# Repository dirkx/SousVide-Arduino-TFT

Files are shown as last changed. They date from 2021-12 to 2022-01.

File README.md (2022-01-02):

# Sousvide controller

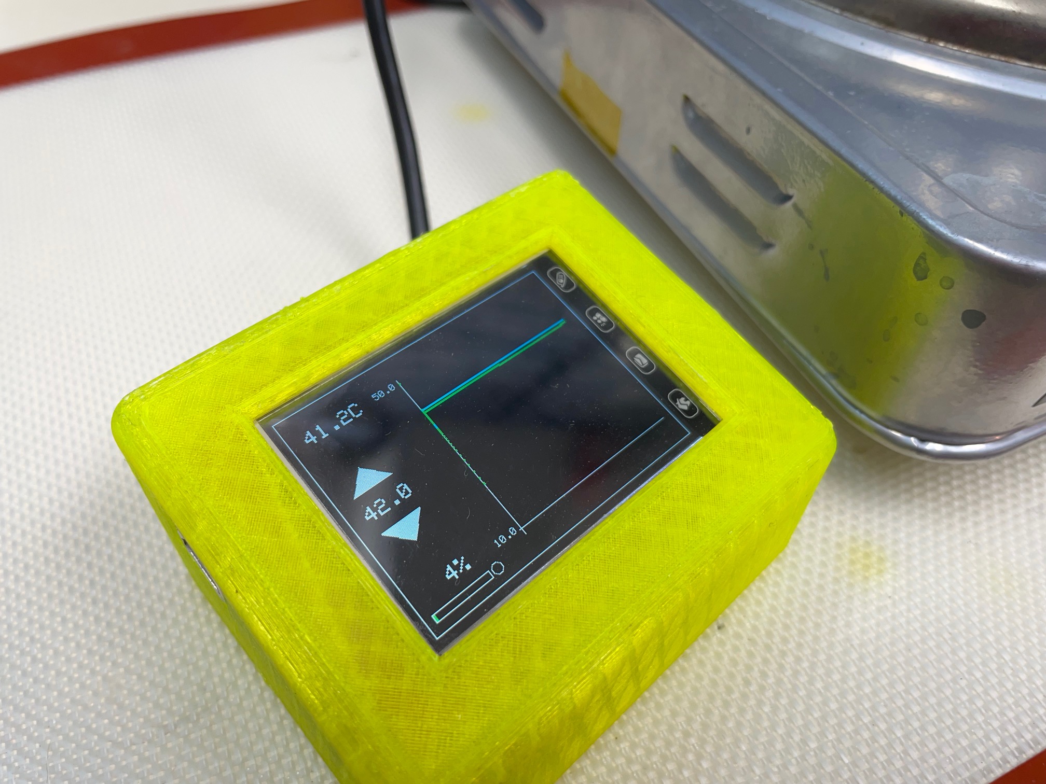
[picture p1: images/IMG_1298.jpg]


# Parts/Bill of material

Prices shown below are just the `first hit` on duckduckgo; if you shop around a bit - you may well get much lower prices on Aliexpress.

1. Hotplate, € 9.99 https://www.obelink.nl/tristar-kp-6185-kookplaat.html
2. Solid state relay € 5-10 euro; 16 Ampere https://www.amazon.nl/-/en/dp/B09F9WK7JP/ref=sr_1_14
3. Arduino UNO https://www.kiwi-electronics.nl/nl/arduino-uno-rev3-atmega328-729
4. 2.4 inch TFT screen € 5-10 https://www.aliexpress.com/item/32923876240.html
5. Waterproof Temperature sensor: € 2-5 https://www.hobbyelectronica.nl/product/ds18b20-waterdicht/ or alternatively the https://www.amazon.nl/MAX6675-Temperatuur-Thermokoppel-Schroef-Arduino/dp/B07Y9YJ3HG/ref=sr_1_5 for a wider range.
6. Some 5 volt adaptor € 2-3 https://nl.aliexpress.com/item/1005001863054181.html
7. Any 10-22 k resistor (1/16 watt or more)
 
# Wiring

The trick here is that we continue use the original knob and temperature safeties. So these still set a 'max'.

## before

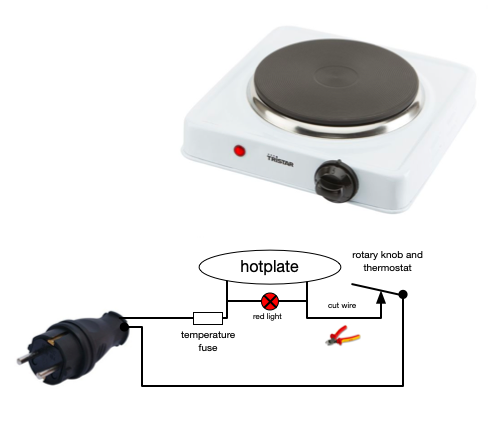
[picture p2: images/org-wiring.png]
Wiringt Wiring before


The intend is to also snip, rather than bypass or bridge, the origianal termo controlled switch.

## after
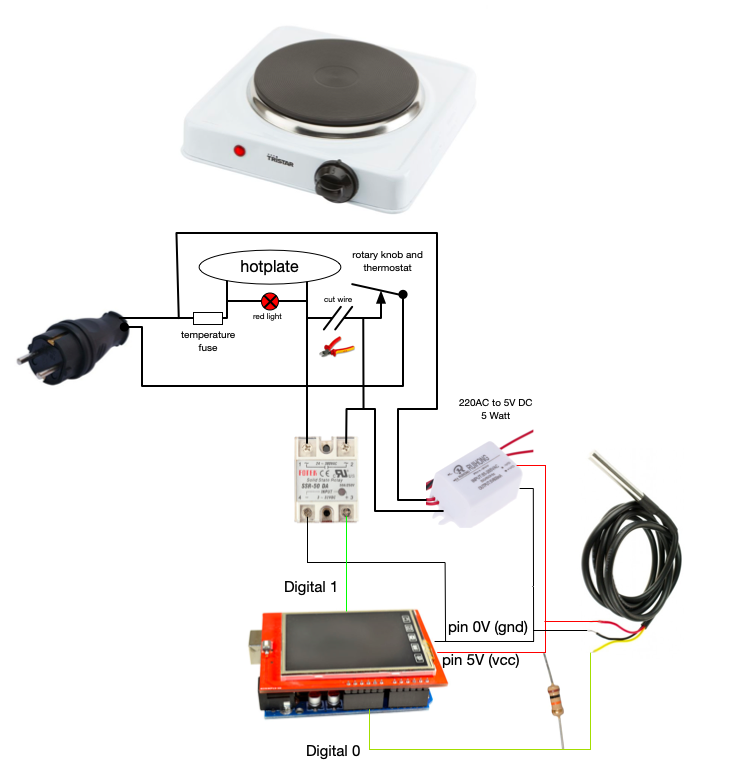
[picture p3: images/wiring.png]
Wiringt Wiring after


When mounting the SSR inside the case - note that there is one area that is nicely 'flat' (under the sticker). So it is best to mount here; as that means that the whole casing becomes a bit of a heatsink too.

# Enclosure

## OpenSCAD version

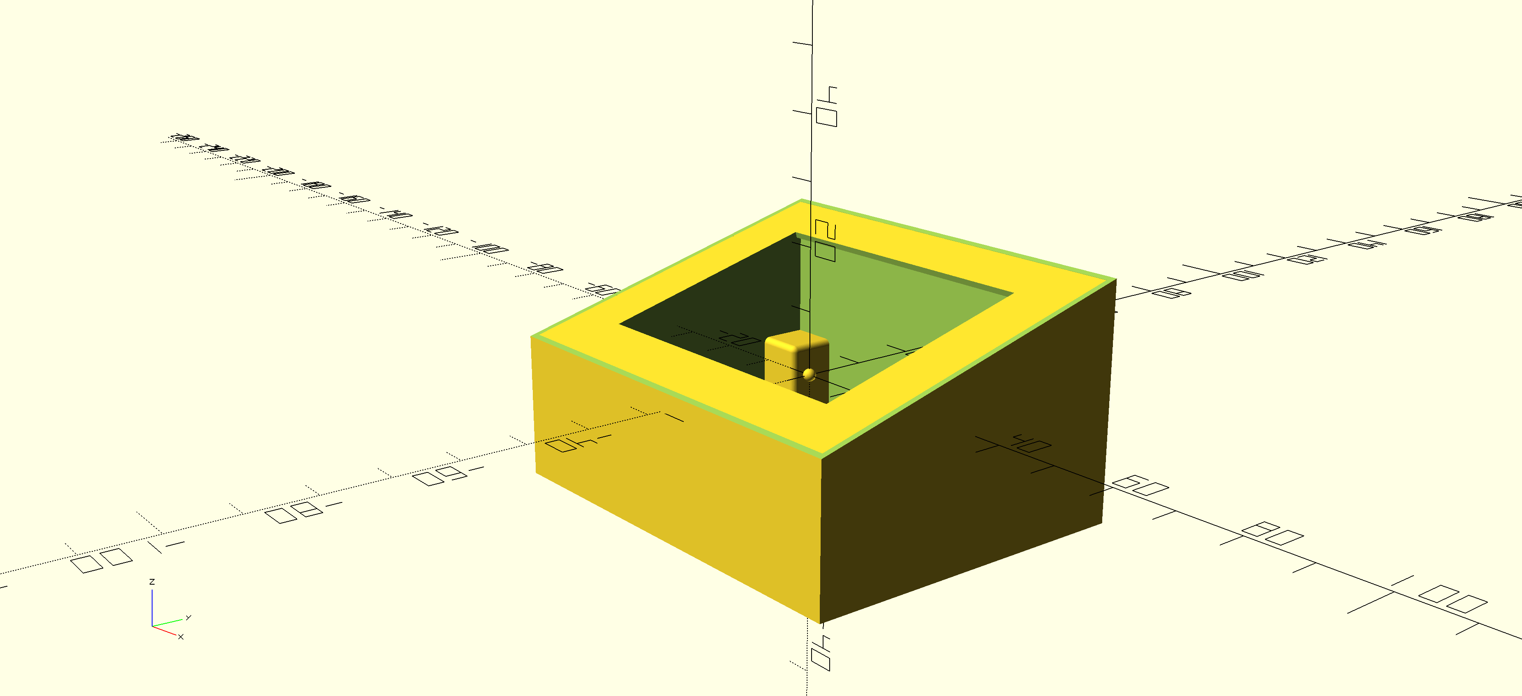
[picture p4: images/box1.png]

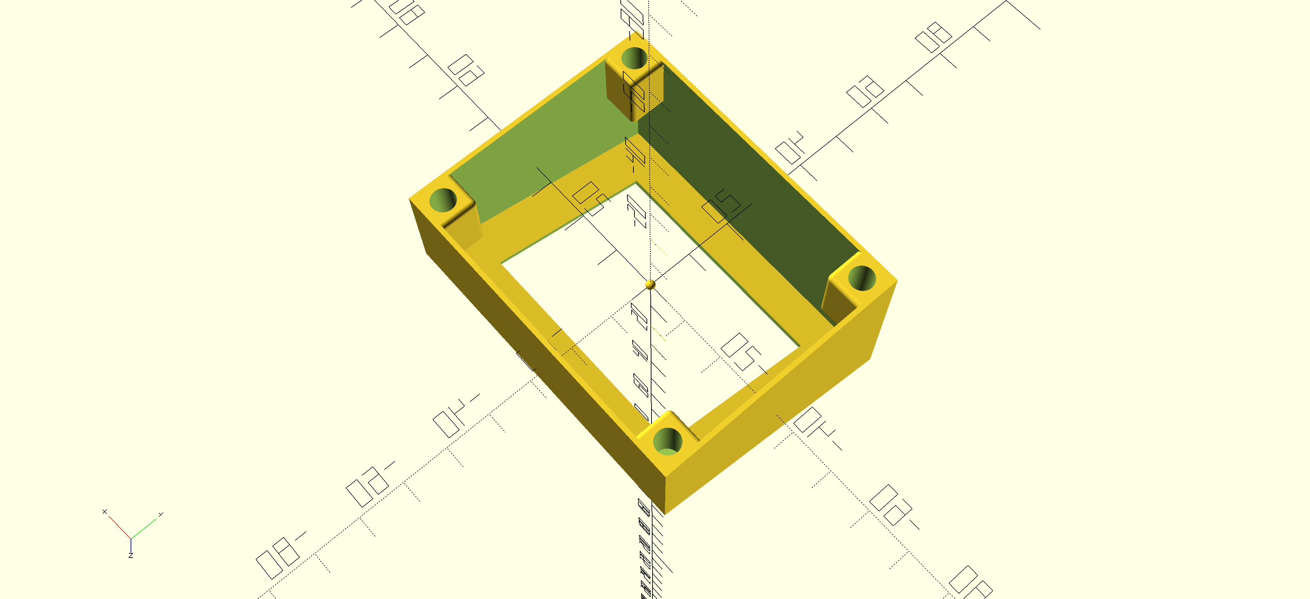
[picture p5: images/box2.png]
Box botom Box bottom


## STEP/Fusion version

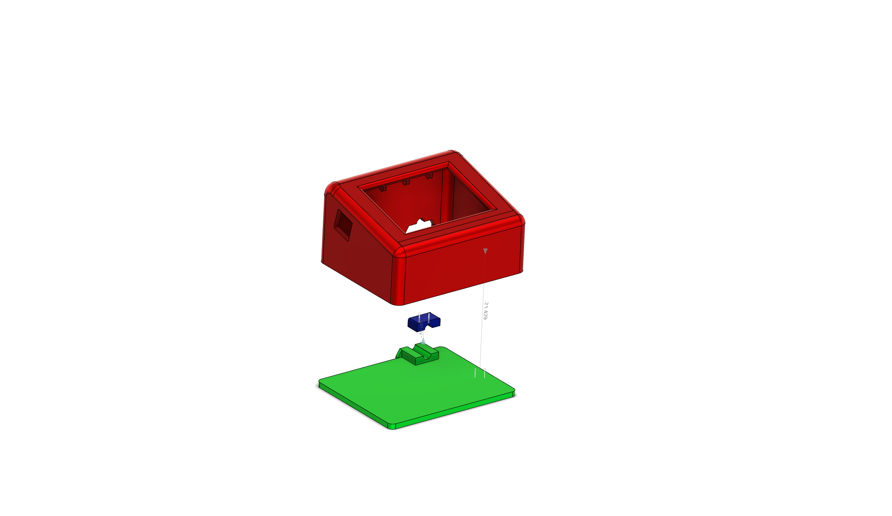
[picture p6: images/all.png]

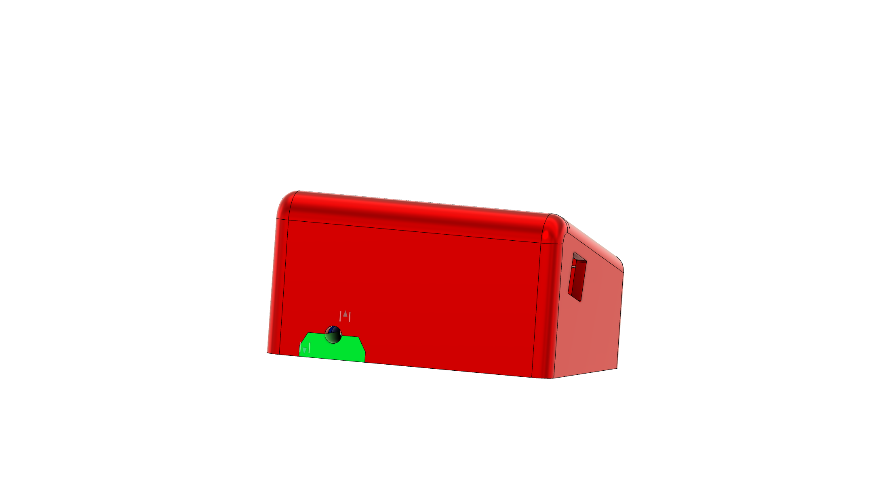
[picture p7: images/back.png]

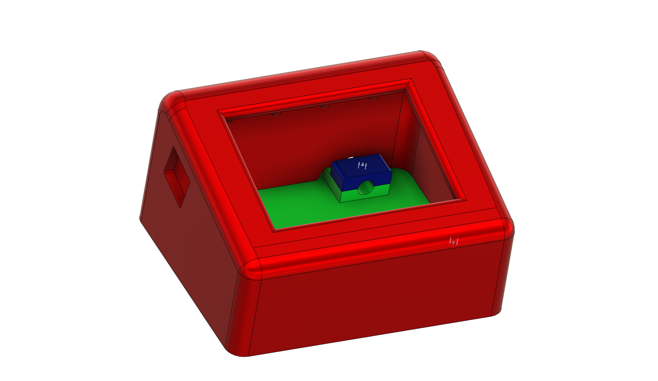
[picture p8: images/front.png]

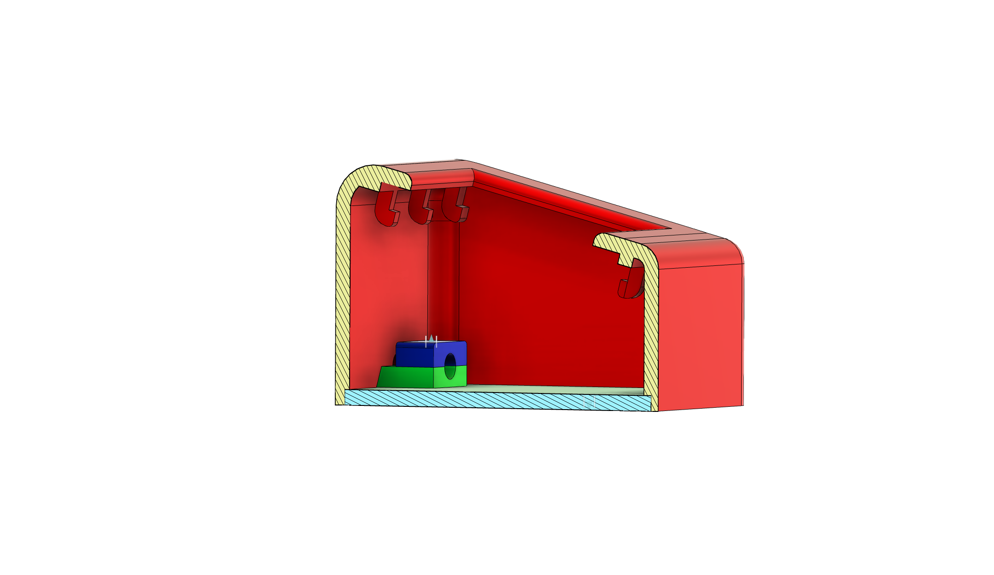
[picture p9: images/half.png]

Box top
Box top

# Result

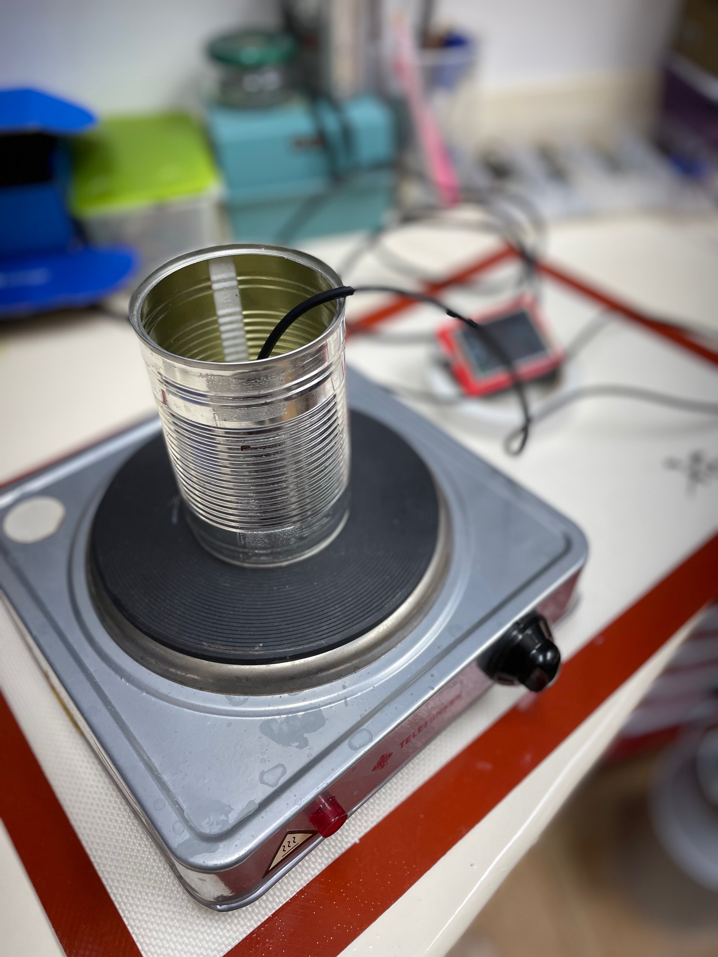
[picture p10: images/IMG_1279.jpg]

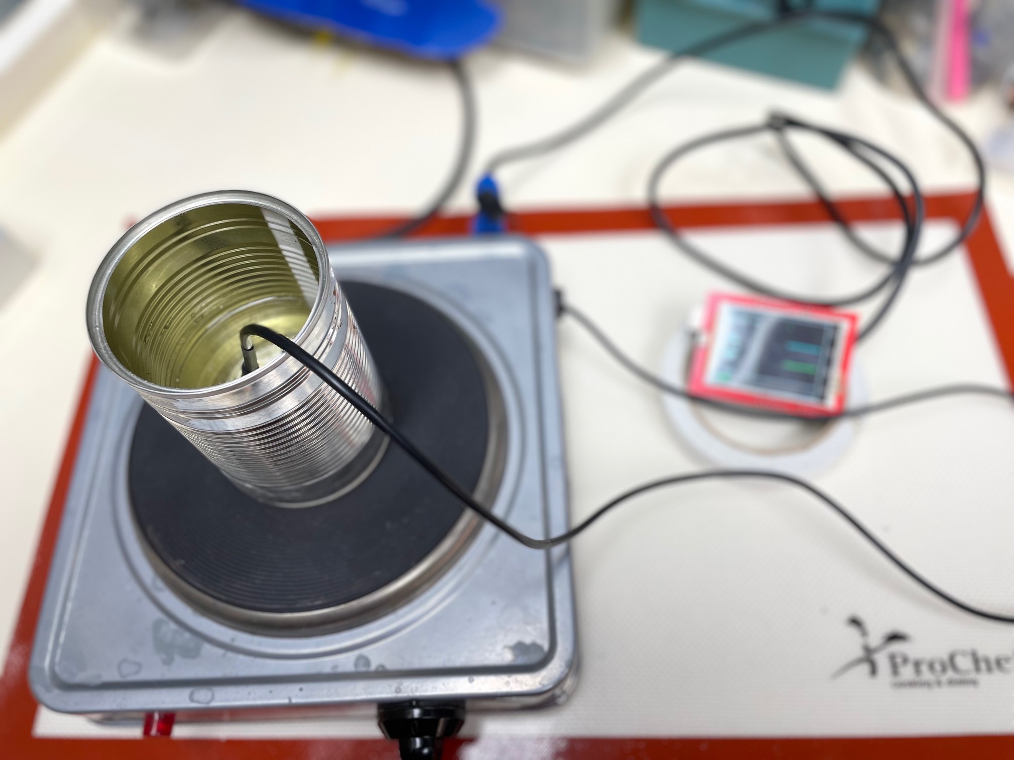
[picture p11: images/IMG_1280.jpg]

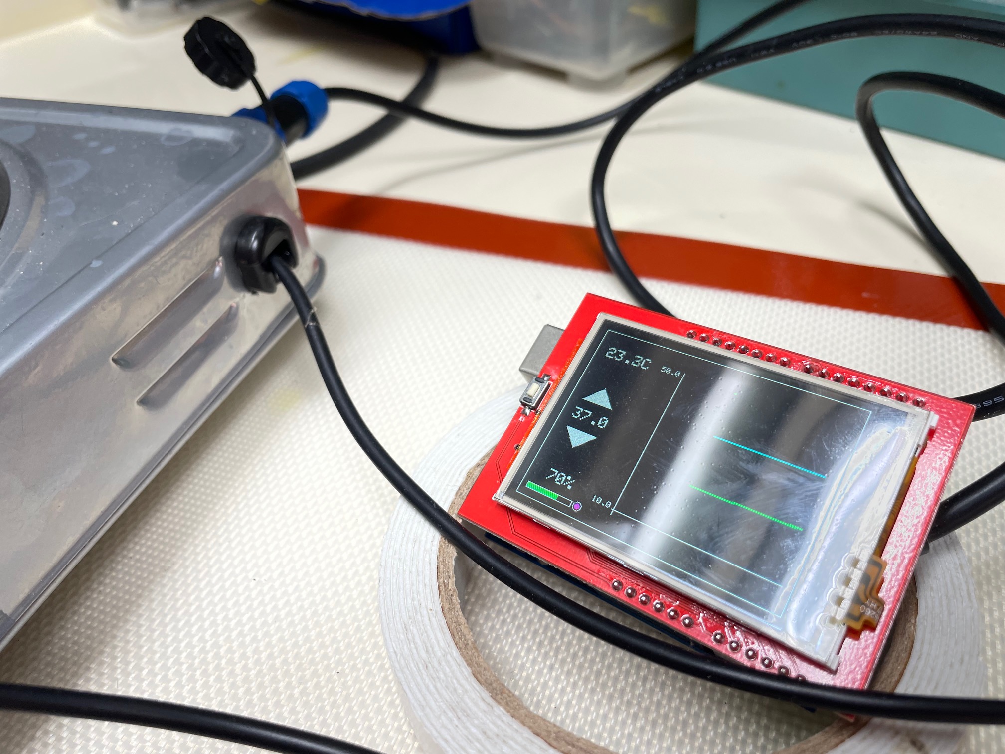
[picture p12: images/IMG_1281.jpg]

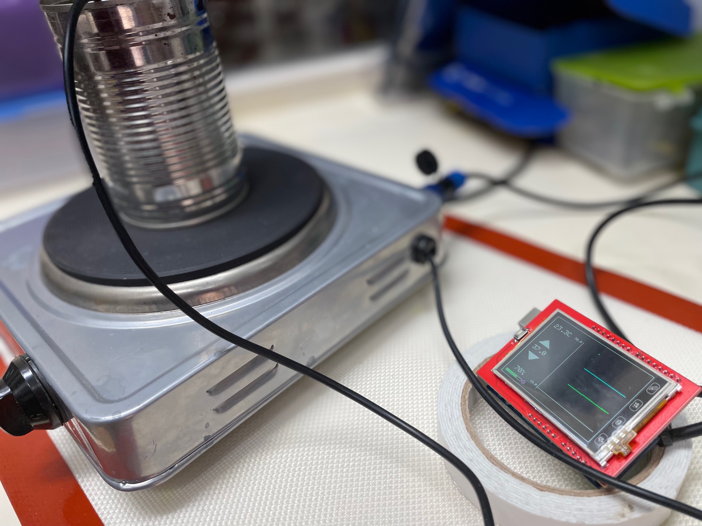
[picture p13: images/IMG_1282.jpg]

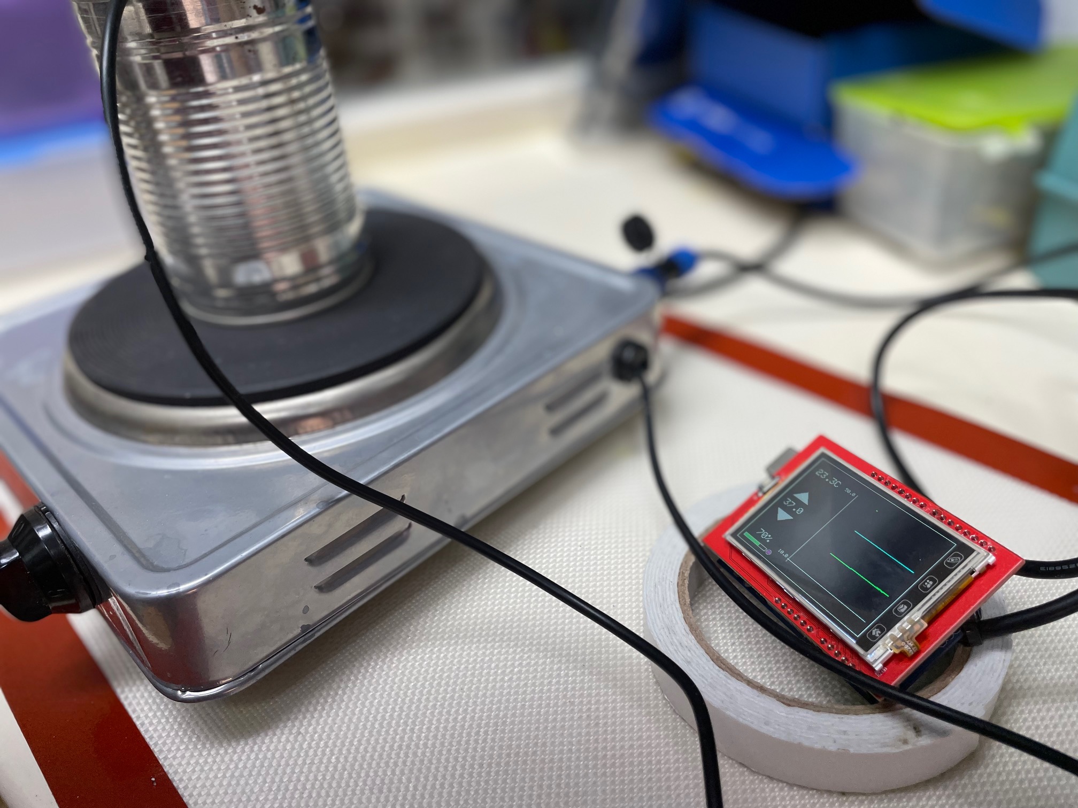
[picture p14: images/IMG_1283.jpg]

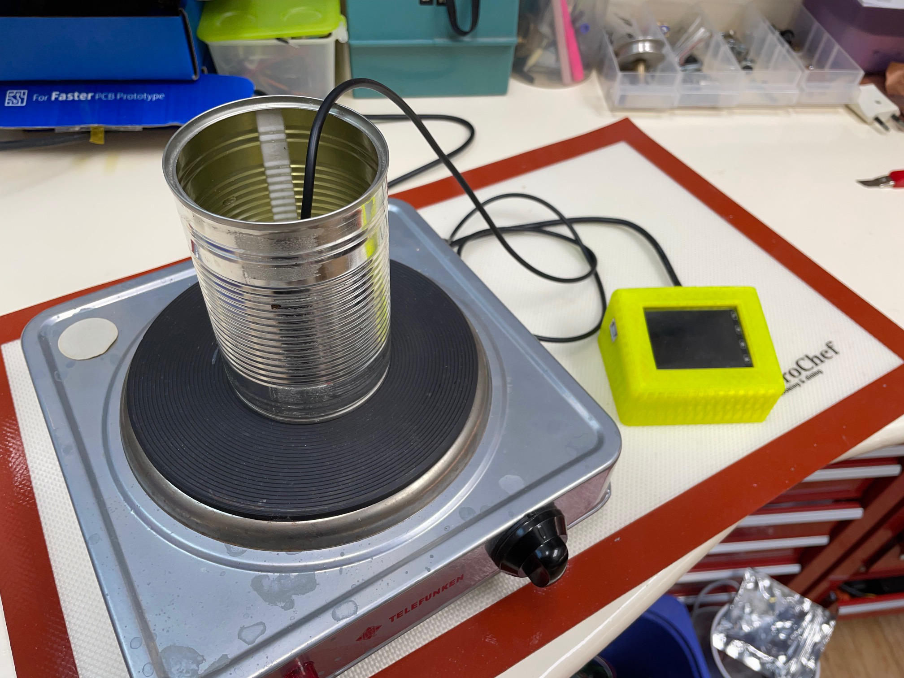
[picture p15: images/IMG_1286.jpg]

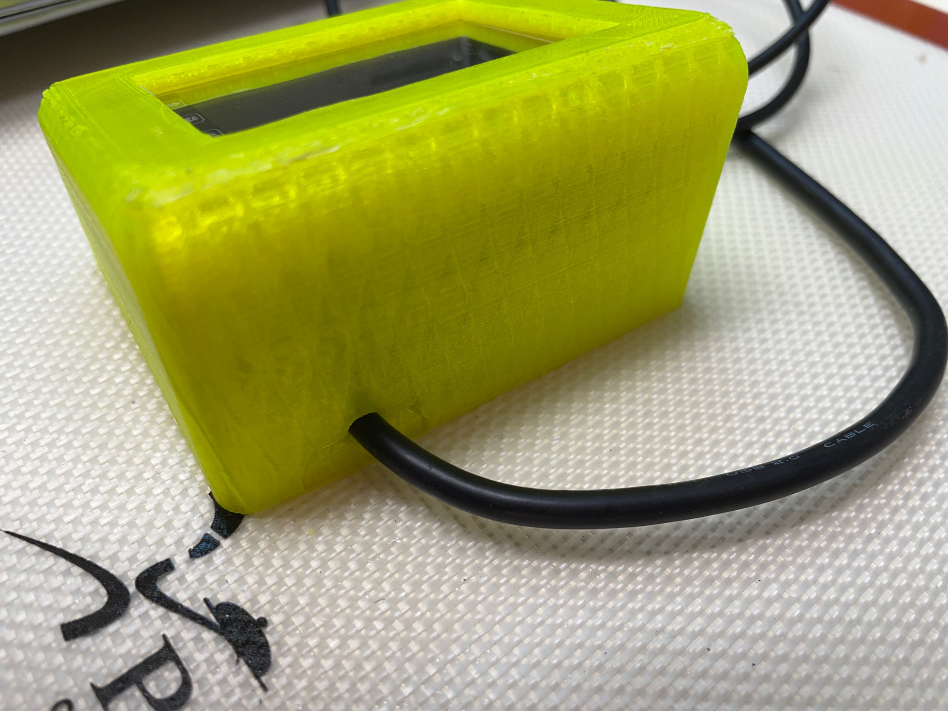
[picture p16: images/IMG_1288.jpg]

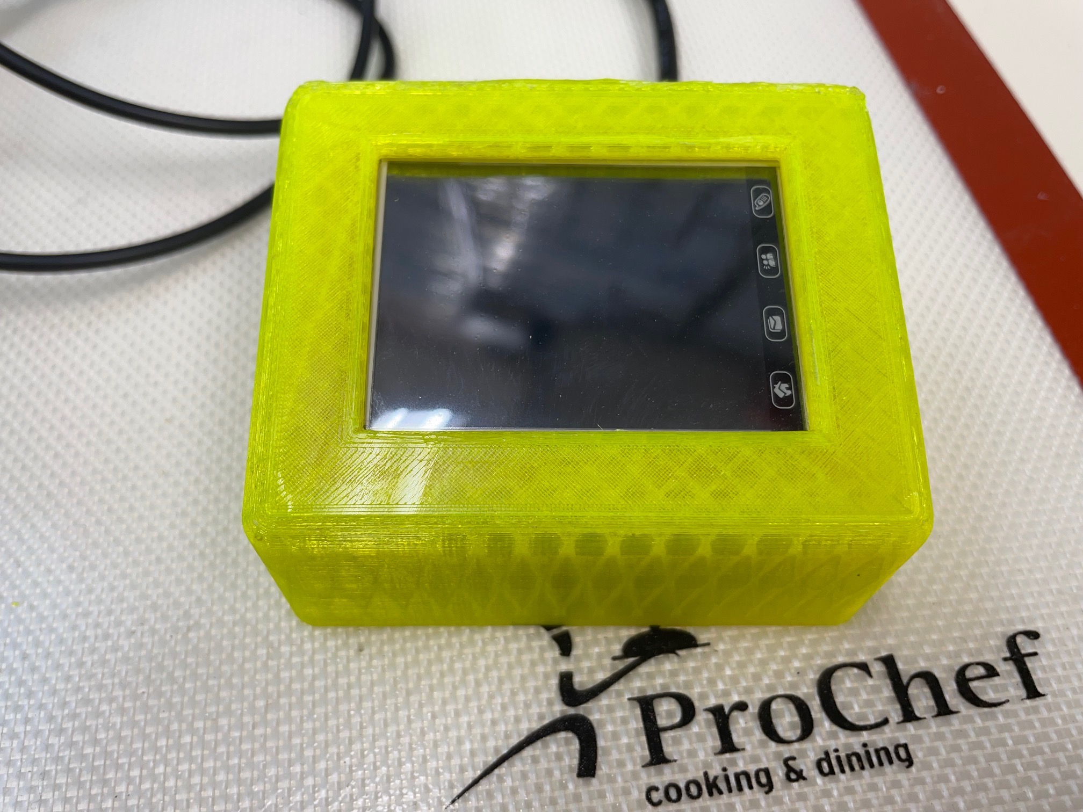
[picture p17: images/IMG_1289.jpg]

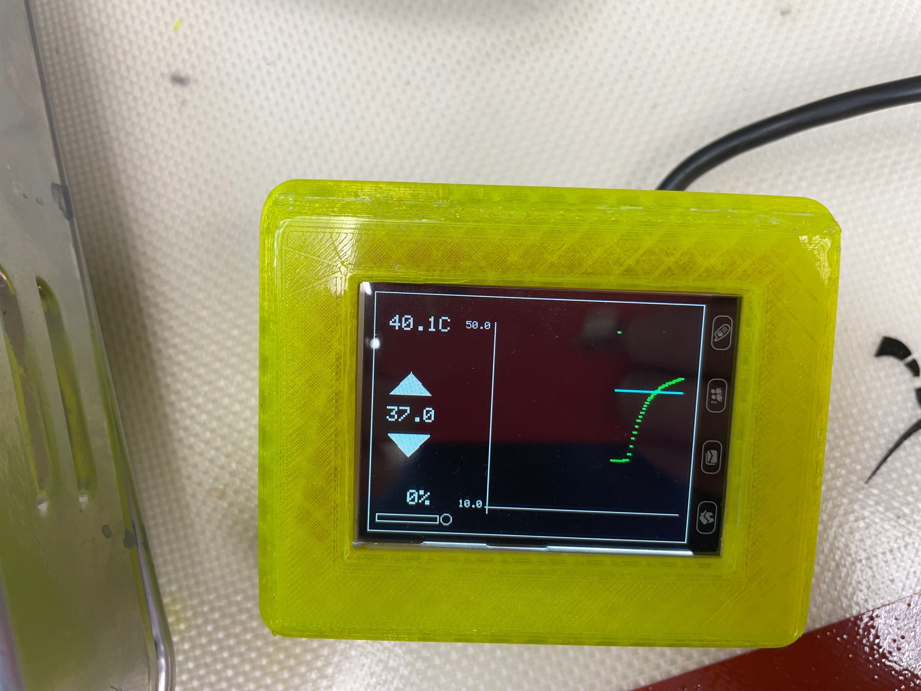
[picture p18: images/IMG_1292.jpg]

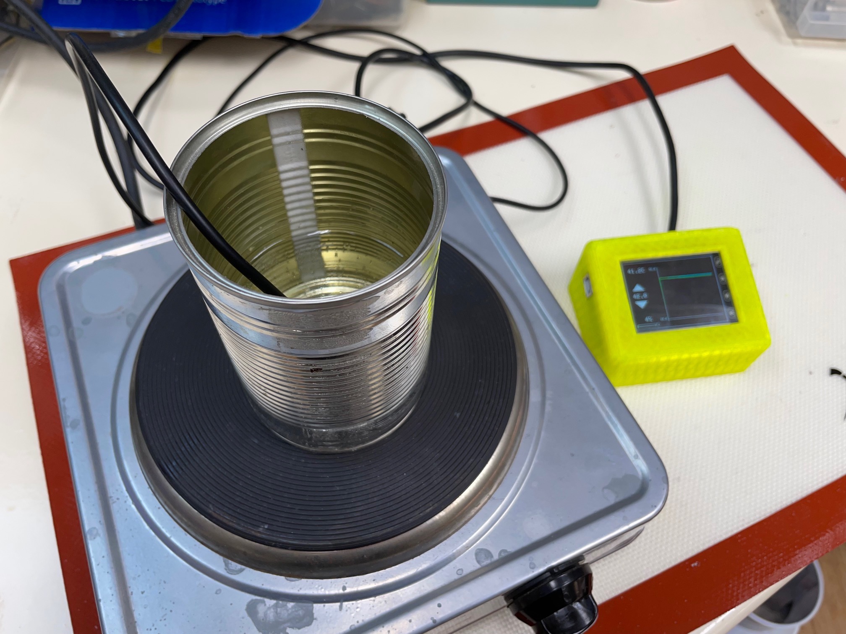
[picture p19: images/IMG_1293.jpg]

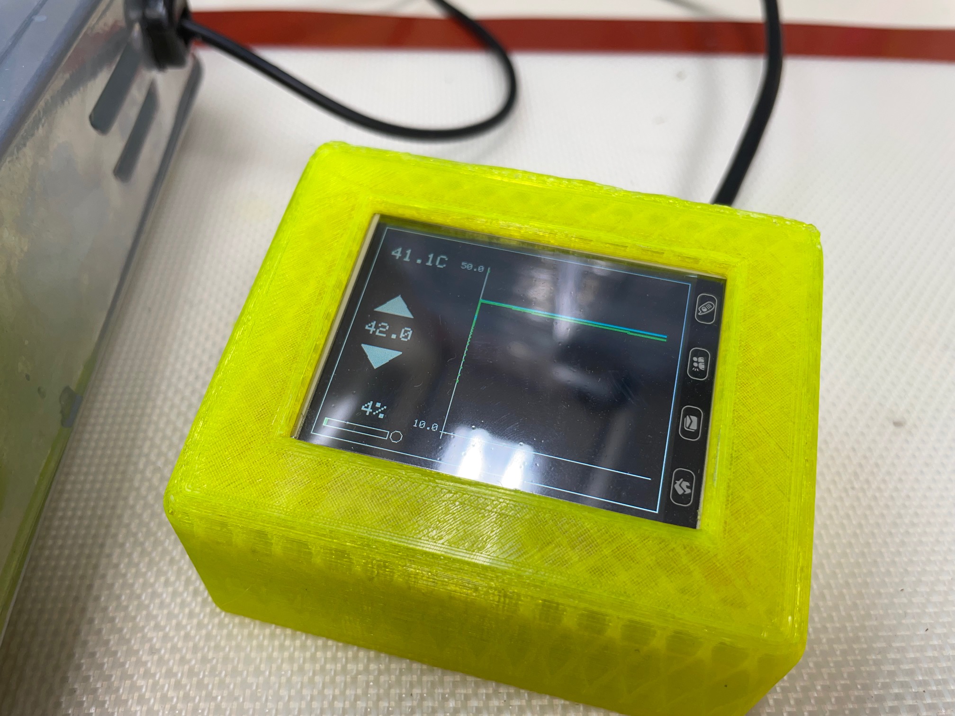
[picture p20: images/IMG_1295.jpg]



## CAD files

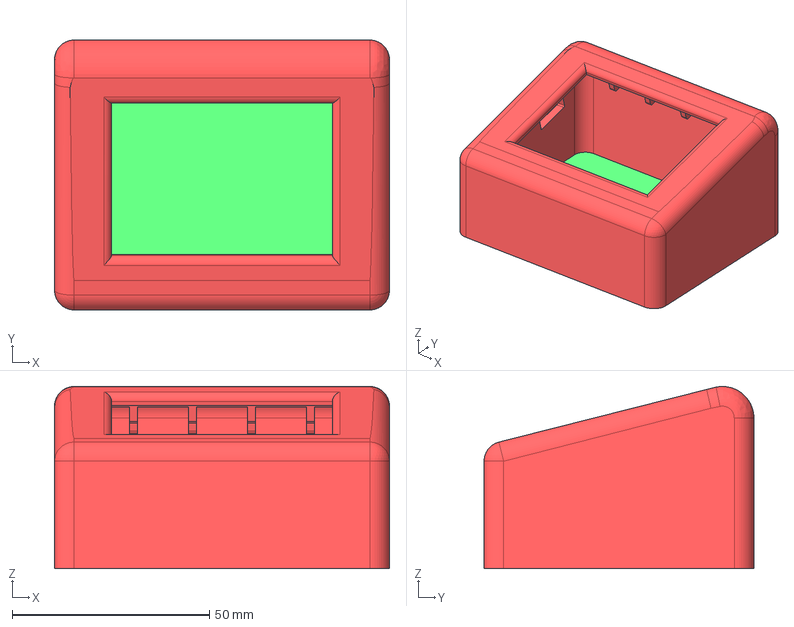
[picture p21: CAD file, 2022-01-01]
enclosure-sous-vide-v1.06.step
85.0 x 68.5 x 46.2 mm
hull
floor
klemblokje

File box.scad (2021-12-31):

screen_mod_x=72.5; 
screen_mod_y=52.7;

screen_x=50;
screen_y=37;

uno_x=69;
uno_y=53.5;

height=40;

wall=1;
insert=5;

W=max(screen_x, uno_x) + wall * 2;
H=max(screen_y, uno_y) + wall * 2;

$fn=50;

module screwinsert() {
   difference() {
    minkowski() {
         cube([insert+2*wall, insert+2*wall,2.5*insert]);
         sphere(r=wall);
    };
    translate([insert/2+wall,insert/2+wall,insert-wall]) cylinder(r=insert/2,2.5*insert,center=true);
};
 };
 
module box(h=height,offset=-wall*2) {
    union() {
    difference()  {
        cube([W,H,h], center=true);
        translate([0,0,offset]) cube([W-2*wall,H-2*wall,2*h], center=true);
    };
};   
}

module topbox() {
    
difference(h=wall) {
    box(h);
    translate([0,0,h/2-wall]) cube([screen_x,screen_y,3*wall], center=true);
};
};

module bottombox() {
   union() {
   box(height,-10);
   translate([-W/2+wall,-H/2+wall,-height/2+wall]) screwinsert();
   translate([-W/2+wall,+H/2-insert-3*wall,-height/2+wall]) screwinsert();
   translate([+W/2-insert-3*wall,-H/2+wall,-height/2+wall]) screwinsert();
   translate([+W/2-insert-3*wall,+H/2-insert-3*wall,-height/2+wall]) screwinsert();
    };
 }
 
module all() {
difference() {
    union() { 
        bottombox(); 
        translate([0,0,10]) rotate([15,0,0]) topbox(); 
    };
    translate([0,0,31.22325]) rotate([15,0,0]) cube([2*W,2*H,height], center=true);

 };
 };
 
 { all(); sphere(r=1); };

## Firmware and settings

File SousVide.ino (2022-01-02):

/* Copyright 2011, 2021 Dirk-Willem van Gulik, alle rights reserved.

    Licensed under the Apache Software Licenses version 2.0 or newer.
*/
#include <Adafruit_GFX.h>    // Core graphics library

// #define ADA
#ifdef ADA
// Fancier Blue boards with thje M3 holes from Adafruit / kiwielectronics.
//
#include <Adafruit_TFTLCD.h>
#else
// Red boards with "white price" sticker on the back from unknown
// provenance and odd white icons on the silkscreen.
//
#include "MCUFRIEND_kbv.h"
#endif
#include <TouchScreen.h>
#include <PID_v1.h>


// When using the BREAKOUT BOARD only, use these 8 data lines to the LCD:
// For the Arduino Uno, Duemilanove, Diecimila, etc.:
//   D0 connects to digital pin 8  (Notice these are
//   D1 connects to digital pin 9   NOT in order!)
//   D2 connects to digital pin 2
//   D3 connects to digital pin 3
//   D4 connects to digital pin 4
//   D5 connects to digital pin 5
//   D6 connects to digital pin 6
//   D7 connects to digital pin 7

// For the Arduino Mega, use digital pins 22 through 29
// (on the 2-row header at the end of the board).
//   D0 connects to digital pin 22
//   D1 connects to digital pin 23
//   D2 connects to digital pin 24
//   D3 connects to digital pin 25
//   D4 connects to digital pin 26
//   D5 connects to digital pin 27
//   D6 connects to digital pin 28
//   D7 connects to digital pin 29

// For the Arduino Due, use digital pins 33 through 40
// (on the 2-row header at the end of the board).
//   D0 connects to digital pin 33
//   D1 connects to digital pin 34
//   D2 connects to digital pin 35
//   D3 connects to digital pin 36
//   D4 connects to digital pin 37
//   D5 connects to digital pin 38
//   D6 connects to digital pin 39
//   D7 connects to digital pin 40


#define RELAY_1PERC_ON (100 /* milliseconds */)
#define RELAY 1 /* GPIO pin */
#define RELAY_ON HIGH

# // LCD
#define LCD_CS A3
#define LCD_CD A2 /* aka as RS */
#define LCD_WR A1
#define LCD_RD A0
#define LCD_RESET A4


// Sensor to use DS18B20 or MAX6675
//
// #define MAX6675
#define DS18B20
// #define MOCKSENSOR // will also mock the relay / not really switch it on.

#define LED (13)

unsigned long tempSampleTimeInMillies;

class Log : public Print {
  public:
    Log() {
      // Serial.begin(115200);
    }
    virtual size_t write(uint8_t c);
  private:
};

size_t Log::write(uint8_t c) {
  // return Serial.write(c);
  return 1;
}

Log Log;

#ifdef DS18B20
// Temperatue sensor and relay
#include <OneWire.h>
#include <DallasTemperature.h>
#define ONE_WIRE_BUS 0
#define RESOLUTION 12

OneWire oneWire(ONE_WIRE_BUS);
DallasTemperature sensors(&oneWire);

bool setup_temp() {
  sensors.begin();
  DeviceAddress tempDeviceAddress;
  sensors.getAddress(tempDeviceAddress, 0);
  if (!sensors.validAddress(tempDeviceAddress)) {
    Log.println("Alert - no sensor found");
    return false;
  }
  sensors.setResolution(tempDeviceAddress, RESOLUTION);

  sensors.setWaitForConversion(false);
  sensors.requestTemperatures(); // que one up.
  tempSampleTimeInMillies = 750 / (1 << (12 - RESOLUTION));

  Log.print("Wired temperature to i2c; dallas address:");
  for (int i = 0; i < 8; i++) {
    if (tempDeviceAddress[i] < 16)
      Log.print(0, HEX);
    Log.print(tempDeviceAddress[i], HEX);
  };
  Log.println("\n");
  return true;
}

float get_temp() {
  float t = sensors.getTempCByIndex(0);
  sensors.requestTemperatures(); // que the next one up (to be feched in tempSampleTimeInMillies).
  return t;
}
#endif

#ifdef MAX6675
#include <Thermocouple.h>
#include <MAX6675_Thermocouple.h>
#include <AverageThermocouple.h>

#define SCK_PIN 3
#define CS_PIN 4
#define SO_PIN 5

#define READINGS_NUMBER 10
#define DELAY_TIME 10
Thermocouple* thermocouple = NULL;

void setup_temp() {
  Thermocouple* originThermocouple = new MAX6675_Thermocouple(SCK_PIN, CS_PIN, SO_PIN);
  thermocouple = new AverageThermocouple(
    originThermocouple,
    READINGS_NUMBER,
    DELAY_TIME
  );
  tempSampleTimeInMillies = DELAY_TIME * READINGS_NUMBER;
}

float get_temp() {
  return thermocouple->readCelsius();

}
#endif

#ifdef MOCKSENSOR
void setup_temp() {
  tempSampleTimeInMillies = 500;
}

float get_temp() {
  return 30.0 + 10 * sin(millis() / 5000.);
}
#endif

// Resistors touch screen.

#define YP A1  // must be an analog pin, use "An" notation!
#define XM A2  // must be an analog pin, use "An" notation!
#define YM 7   // can be a digital pin
#define XP 6   // can be a digital pin

#define PENRADIUS 3

#define TS_MINX 150
#define TS_MINY 120
#define TS_MAXX 920
#define TS_MAXY 940

// For better pressure precision, we need to know the resistance
// between X+ and X- Use any multimeter to read it
// For the one we're using, its 300 ohms across the X plate
TouchScreen ts = TouchScreen(XP, YP, XM, YM, 300);


// Assign human-readable names to some common 16-bit color values:
#define BLACK   0x0000
#define BLUE    0x001F
#define RED     0xF800
#define GREEN   0x07E0
#define CYAN    0x07FF
#define MAGENTA 0xF81F
#define YELLOW  0xFFE0
#define WHITE   0xFFFF

#define RGB(r, g, b) (((r&0xF8)<<8)|((g&0xFC)<<3)|(b>>3))

#define GREY      RGB(127, 127, 127)
#define DARKGREY  RGB(64, 64, 64)
#define TURQUOISE RGB(0, 128, 128)
#define PINK      RGB(255, 128, 192)
#define OLIVE     RGB(128, 128, 0)
#define PURPLE    RGB(128, 0, 128)
#define AZURE     RGB(0, 128, 255)
#define ORANGE    RGB(255,128,64)

// LCD orientation: always landscape, 1=USB upper left / 3=USB lower right
//
#define LCDROTATION 1

#define SET_SIZE  10
#define SET_X     SET_SIZE + 2 * SET_SIZE + 8
#define SET_Y     tft.height() / 2

#define ACT_SIZE    SET_SIZE
#define ACT_X       SET_X
#define ACT_Y       30

float   setTemp = 37.00;

#ifdef ADA
Adafruit_TFTLCD tft(LCD_CS, LCD_CD, LCD_WR, LCD_RD, LCD_RESET);
#else
MCUFRIEND_kbv tft(LCD_CS, LCD_CD, LCD_WR, LCD_RD, LCD_RESET);
#endif

int GRAPH_X, GRAPH_W, GRAPH_Y, GRAPH_H, PWR_X, PWR_Y, PWR_H, PWR_W, DX;

const float MIN_T = 10.;
const float MAX_T = 50.;

const int N = 128;

float   temp[N], setTempHistory[N];

// double kp=2,ki=0.5,kd=2;

// 5 minuten 15 -> 37graden; overshoot to 60; 4 min.
// Dan 8-10 minuten flat. Daling 0.2/10 seconden. Bij 50C 0.2/15 seconden.
//
// 0 and 100% change rates.
//
#define DOWNRATE (0.2/15)    // Daalt ron de 0.1-0.2 per 10-15 seconden.
#define UPRATE ((60-16)/600) // van 15->16 graden in ongeveer 10 minuten.

// double consKp = 10, consKi = 0.05, consKd = 0;
double consKp = 5, consKi = 0.01, consKd = 3.0;
double Setpoint, Input, Output;

PID myPID(&Input, &Output, &Setpoint, consKp, consKi, consKd, DIRECT);

void setup(void) {
  // Serial.begin(115200);
  // while (!Serial) {};
  Log.println("\n\nStarted " __FILE__ "\n" __DATE__ " " __TIME__);
  tft.reset();

  digitalWrite(RELAY, !RELAY_ON);
  pinMode(RELAY, OUTPUT);
  digitalWrite(RELAY, !RELAY_ON);

  uint16_t identifier = tft.readID();
  if (!identifier)
    Log.println(F("No LCD driver found"));
  else {
    Log.print(F("LCD driver chip: 0x"));
    Log.println(identifier, HEX);
  }

  tft.begin(identifier);
  tft.setRotation(LCDROTATION);

  // We cannot '#define' or const-optimize these; as the tft size
  // and orientation is only known post setup.
  //
  GRAPH_X = 120;
  GRAPH_W = (tft.width() - GRAPH_X - 16);

  GRAPH_Y = 30;
  GRAPH_H  = (tft.height() - GRAPH_Y - 32);

  PWR_X = SET_SIZE;
  PWR_W = (60);
  PWR_H = (6);
  PWR_Y = (tft.height() - 12 - PWR_H);

  DX = GRAPH_W / N + 1;

  tft.fillScreen(BLACK);
  tft.drawRect(1, 1, tft.width() - 2, tft.height() - 2, WHITE);


  tft.fillTriangle(SET_X - 2 * SET_SIZE, SET_Y + 2 * SET_SIZE,
                   SET_X + 2 * SET_SIZE, SET_Y + 2 * SET_SIZE,
                   SET_X, SET_Y + 4.2 * SET_SIZE,
                   WHITE);
  tft.fillTriangle(SET_X - 2 * SET_SIZE, SET_Y - 2 * SET_SIZE,
                   SET_X + 2 * SET_SIZE, SET_Y - 2 * SET_SIZE,
                   SET_X, SET_Y - 4.2 * SET_SIZE,
                   WHITE);


  tft.drawLine(GRAPH_X - 2, GRAPH_Y - 4,
               GRAPH_X - 2, GRAPH_Y + GRAPH_H + 8,
               WHITE);
  tft.drawLine(GRAPH_X - 4,             GRAPH_Y + GRAPH_H  + 2,
               GRAPH_X + GRAPH_W + 4, + GRAPH_Y + GRAPH_H  + 2,
               WHITE);

  char buff[10];

  tft.setTextColor(WHITE, BLACK);
  tft.setTextSize(1);

  tft.setCursor(GRAPH_X - 30, GRAPH_Y - 4 + GRAPH_H);
  snprintf(buff, sizeof(buff), "%02d.%01d", (int)MIN_T, ((int)(10 * MIN_T)) % 10);
  tft.print(buff);

  tft.setCursor(GRAPH_X - 30, GRAPH_Y - 4);
  snprintf(buff, sizeof(buff), "%02d.%01d", (int)MAX_T, ((int)(10 * MAX_T)) % 10);
  tft.print(buff);

  tft.drawRect(PWR_X - 1, PWR_Y - 1,
               PWR_W + 2, PWR_H + 2,
               WHITE);

  myPID.SetMode(AUTOMATIC);
  myPID.SetOutputLimits(0, 100);


  updateSetTemp(setTemp);
  if (!setup_temp()) {
    tft.setCursor(tft.width() / 2, tft.height() / 2);
    tft.setTextColor(WHITE, BLACK);
    tft.setTextSize(SET_SIZE / 4);
    tft.print("NO sensor");
    while (1) {
      delay(500);
      digitalWrite(LED, !digitalRead(LED));
    }
  }
  updateTemp(13.2);

  pinMode(LED, OUTPUT);
}

void updateSetTemp(float f) {
  char buff[10];

  tft.setCursor(SET_X - 9 * SET_SIZE / 4 , SET_Y - SET_SIZE / 2 - 2);
  tft.setTextColor(WHITE, BLACK);
  tft.setTextSize(SET_SIZE / 4);
  snprintf(buff, sizeof(buff), "%02d.%01d", (int)f, ((int)(10 * fabs(f))) % 10);
  tft.print(buff);
}

void updateTemp(float f) {
  char buff[10];

  tft.setCursor(ACT_X - 9 * ACT_SIZE / 4 , ACT_Y - ACT_SIZE / 2 - 2);
  tft.setTextColor(WHITE, BLACK);
  tft.setTextSize(ACT_SIZE / 4);
  snprintf(buff, sizeof(buff), "%02d.%01dC", (int)f, ((int)(10 * fabs(f))) % 10);
  tft.print(buff);
}

#define MINPRESSURE 10
#define MAXPRESSURE 1000


void loop()
{
  digitalWrite(LED, HIGH);
  TSPoint q = ts.getPoint();
  TSPoint p = q;
  digitalWrite(LED, LOW);

  // if sharing pins, you'll need to fix the directions of the touchscreen pins
  //pinMode(XP, OUTPUT);
  pinMode(XM, OUTPUT);
  pinMode(YP, OUTPUT);
  //pinMode(YM, OUTPUT);

  static unsigned long pressStarted = 0;
  unsigned long now = millis();

  unsigned long thisPress = 0;
  if (p.z > MINPRESSURE && p.z < MAXPRESSURE) {
    p.x = map(q.x, TS_MINX, TS_MAXX, 0, tft.width());
    p.y = map(q.y, TS_MINY, TS_MAXY, tft.height(), 0);

    if ((p.x > SET_X -  3 * SET_SIZE) &&  (p.x < SET_X +  3 * SET_SIZE)) {
      if ((p.y < SET_Y -  3 * SET_SIZE) && (p.y > SET_Y -  7 * SET_SIZE)) {

        if (now - pressStarted > 300)
          setTemp -= 0.1;

        if (pressStarted && now - pressStarted > 3000)
          setTemp -= 1;

        thisPress = now;
      } else if ((p.y > SET_Y +  3 * SET_SIZE) && (p.y < SET_Y +  7 * SET_SIZE)) {
        if (now - pressStarted > 300)
          setTemp += 0.1;
        if (pressStarted && now - pressStarted > 3000)
          setTemp += 1;

        thisPress = now;
      }
    }

    if (pressStarted == 0)
      pressStarted = thisPress;

    if (thisPress == 0) {
      pressStarted = 0;
    } else {
      if (setTemp > MAX_T)
        setTemp = MAX_T;
      if (setTemp < MIN_T)
        setTemp = MIN_T;
      updateSetTemp(setTemp);
    }


#if 0
    if ((thisPress == 0) && ((p.y - PENRADIUS) > 0) && ((p.y + PENRADIUS) < tft.height())) {
      tft.fillCircle(p.x, p.y, PENRADIUS, RED);
    }
#endif
  }

  static unsigned long lastUpdate = 0;
  if (now - lastUpdate > tempSampleTimeInMillies) {
    float t = get_temp();
    lastUpdate = millis();

    temp[N - 1] = t;

    for (int i = 0; i < N - 1; i++) {
      temp[i] = temp[i + 1];
      setTempHistory[i] = setTempHistory[i + 1];
    }

    temp[N - 1] =  temp[N - 2];

    setTempHistory[N - 1] = setTemp;
    updateTemp( temp[N - 1]);

    for (int i = 0; i < N; i++) {
      float t = temp[i];

      if (t < MIN_T) t = MIN_T;
      if (t > MAX_T) t = MAX_T;

      t = (t - MIN_T) / (MAX_T - MIN_T);

      int x = GRAPH_X + GRAPH_W * i / N;
      int y = GRAPH_Y + GRAPH_H * (1. - t);

      t = (setTempHistory[i] - MIN_T) / (MAX_T - MIN_T);
      int sety = GRAPH_Y + GRAPH_H * (1. - t);

      tft.drawFastVLine(x, GRAPH_Y , GRAPH_H + 1, BLACK);
      tft.drawFastVLine(x + 1, GRAPH_Y , GRAPH_H + 1, BLACK);

      if (setTempHistory[i])
        tft.fillRect(x - 2, sety, 4, 2, YELLOW);
      if (temp[i])
        tft.fillRect(x - 2, y, 4, 2, GREEN);
    }
  }


  static unsigned long lastPid = 0;
  if (now - lastPid > 500) {
    Input = temp[N - 1];
    Setpoint = setTemp;
    myPID.Compute();


    tft.fillRect(PWR_X, PWR_Y,
                 PWR_W, PWR_H,
                 BLACK);

    tft.fillRect(PWR_X, PWR_Y,
                 PWR_W * Output / 100. , PWR_H,
                 GREEN);

    tft.fillCircle(PWR_X + PWR_W + 8, PWR_Y - 1 + PWR_H / 2, 3, digitalRead(RELAY) ? MAGENTA : BLACK);
    tft.drawCircle(PWR_X + PWR_W + 8, PWR_Y - 1 + PWR_H / 2, 5, WHITE);

    tft.setCursor(PWR_X + PWR_W / 2 - 25, PWR_Y - 26);
    tft.setTextColor(WHITE, BLACK);
    tft.setTextSize(2);
    char buff[10];

    snprintf(buff, sizeof(buff), "%3d%%  ", (int)Output);
    tft.print(buff);

    lastPid = now;
  }

#if 0
  Log.print("V ");
  Log.print(((now / 500) % 100) / 5);
  Log.print(" -- ");
  Log.println(Output / 5);
#endif

  // If RELAY_1PERC_ON == 500 milli seconds then: switch at least 0.5
  // second; for up to 0.5 x 100 = 50 seconds cycles. Linear (so 10%
  // is 5 second on; 45 seconds off).
  //
  static bool lastState = false;
  if (((int)(now / RELAY_1PERC_ON) % (100)) < (Output)) {
    if (!lastState)
      Log.println("On");
    lastState = true;
#ifndef MOCKSENSOR
    digitalWrite(RELAY, RELAY_ON);
#endif

  } else {
    if (lastState)
      Log.println("off");
    lastState = false;
#ifndef MOCKSENSOR
    digitalWrite(RELAY, !RELAY_ON);
#endif
  }
}

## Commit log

2021-12-31 Add wiring/box images
    [box.scad]
2022-01-01 3D version in STEP and imagesthereof
    [enclosure-sous-vide-v1.06.step]
2022-01-02 Add images and 3d print info, fix wiring diagram
2022-01-02 More wiring explanation.
